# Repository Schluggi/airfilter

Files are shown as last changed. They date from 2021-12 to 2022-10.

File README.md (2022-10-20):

# airfilter 
<a href="https://www.buymeacoffee.com/schluggi" target="_blank">Buy Me A Coffee</a>


> ⚠️ This is a WIP! Some images are missing, but the firmware works fine. 

I've modified my IKEA Förnuftig to work with Home Assistant. After some soldering you can control the filter via MQTT and
also (!) manual with the knob (as originally intended).
I use an ESP32 NodeMCU but an ESP8266 NodeMCU should also work fine.

Via Home Assistant discovery the air filter will show up as a fan-entity with three preset modes `1`, `2` and `3`.
You can also control the fan via the percentage slider.

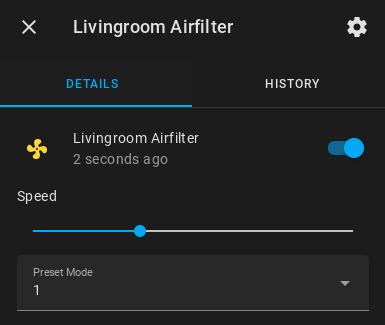
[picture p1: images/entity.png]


## Table of contents
- [Features](https://github.com/Schluggi/airfilter#features)
- [What you need](https://github.com/Schluggi/airfilter#what-you-need)
- [How to](https://github.com/Schluggi/airfilter#how-to)
  - [Flashing](https://github.com/Schluggi/airfilter#flashing)
  - [Teardown](https://github.com/Schluggi/airfilter#teardown)
  - [Soldering and wiring](https://github.com/Schluggi/airfilter#soldering-and-wiring)
- [MQTT](https://github.com/Schluggi/airfilter#mqtt)
- [Home Assistant](https://github.com/Schluggi/airfilter#home-assistant)
- [Questions](https://github.com/Schluggi/airfilter#questions)
- [Credits](https://github.com/Schluggi/airfilter#credits)

## Features
- Control the air filter via MQTT
- Control the air filter manual (as originally intended)
- Home Assistant discovery
  - Support for preset modes
  - Support for percentage control

## What you need
- ESP32 NodeMCU
- 74C14 or 74HC14 Inverter
- 24V to 5V DC/DC-Converter
- Some Jumper Cables
- Superglue
- Soldering iron
- Tiny wires

## How to
### Flashing
Connect the ESP32 NodeMCU via USB to your PC. On Windows you need some additional drivers.
On Linux everything should work out of the box. 
Start the [Arduino IDE](https://www.arduino.cc/en/software) and open the sketch file located at 
`firmware/airfilter/airfilter.ino`.

Change the WiFi and MQTT settings at the top of the file. Then select your NodeMCU (Tools -> Port) and
configure all settings as shown in the screenshot below. Afterwards press flash.
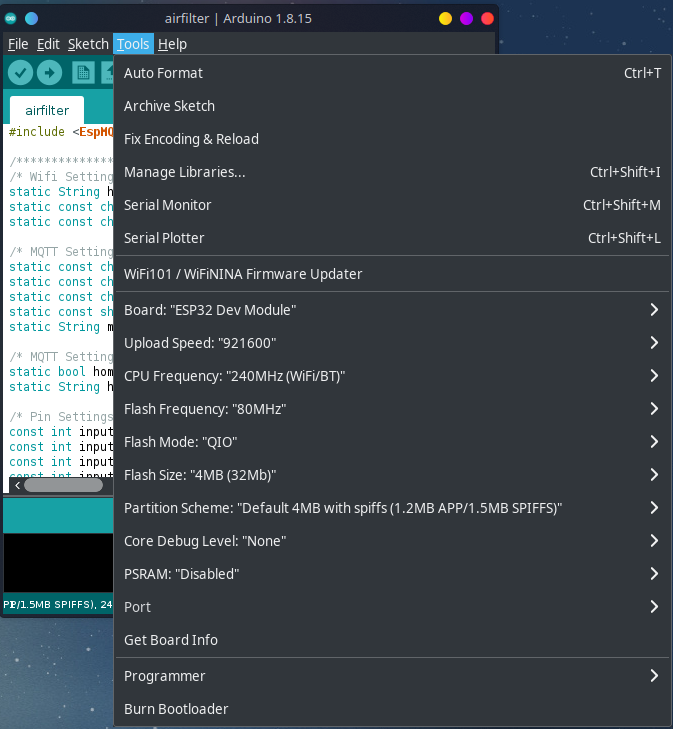
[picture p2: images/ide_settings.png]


### Teardown
Unplug the air filter. 
Remove the blend and the filter. Then unscrew the two phillips screws at the top and remove the plastic part.
Unplug both cables and unscrew the circuit board. You also have to remove the knob before removing the board.

Fortunately IKEA has made a product with a lot of space for us - nice. So we can unscrew the six triangle 
screws and the two phillips screws at the bottom. If you don't have a triangle screwdriver: A slot screwdriver will 
work as well. Then remove the two plastic parts. There are clipped, so make sure not to break anything.
(wip, screw image)

### Soldering and wiring
> **Warning:** This step can not be undone!
 
The knob must not have an effect on the fan speed directly, so we have to cut the circuit path. I've done this with a 
small cutter.
(wip, img cutting)

The internal DC/DC-Converter is sadly not powerful enough to power up the ESP32 (sometimes it works, sometimes not).
So we have to use our own Converter to power up the ESP. Just solder the `GND` and `VIN` pins of the DC/DC-Converter to
the 24V output pin on the circuit board. Connect the `GND` and `VOUT` pins of the DC/DC-Converter to the `VIN` and 
`GND` pins of the ESP.

Connecting the inverter is the hardest part because it's tiny. I've soldered the pins as shown below and then superglued 
the converter onto the board. Not great, but good enough.

#### Wiring
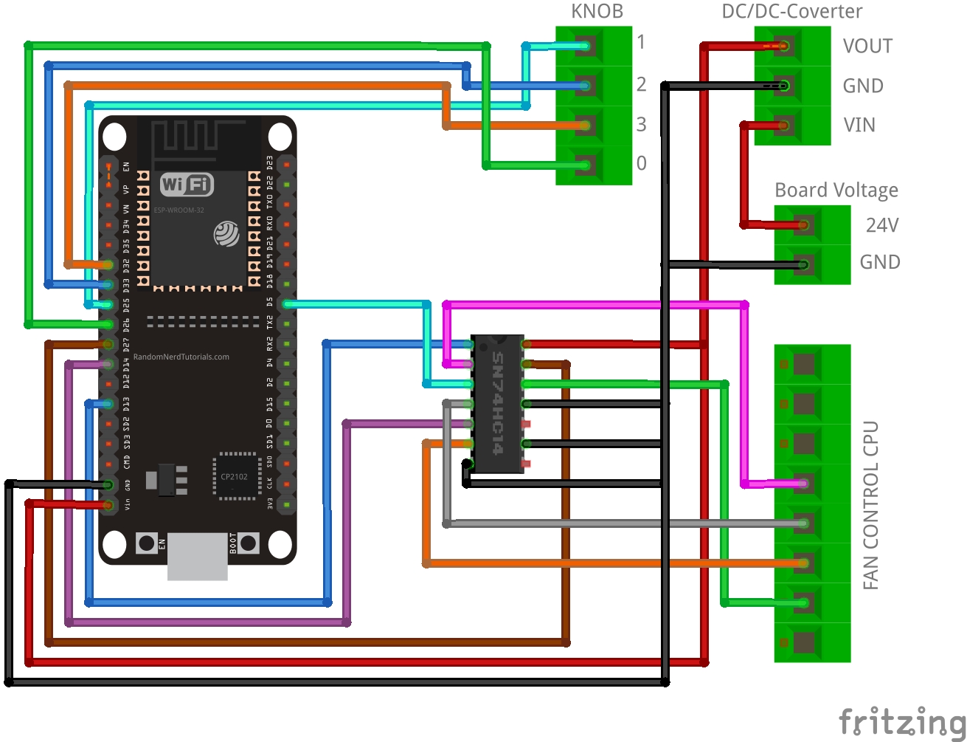
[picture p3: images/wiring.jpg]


This is the fan control CPU. Please mention the origination. 
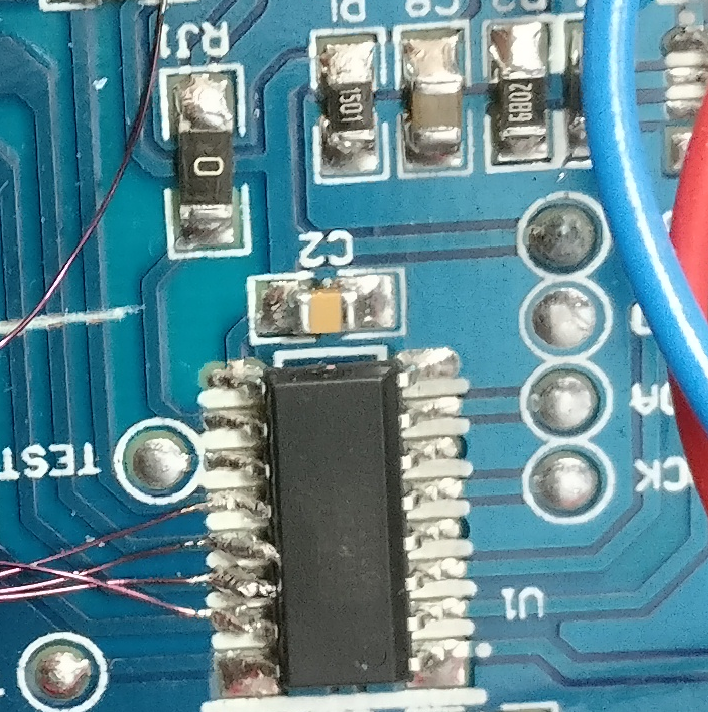
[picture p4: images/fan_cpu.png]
fan_cpu


(wip, img knob connections)

#### Final
> **Caution:** DO NOT USE THIS PHOTO AS REFERENCE! 
> The wiring on this photo looks different from the wiring image because this project
> was learning by doing. So some `GND` and `VCC` wires are connected differently.

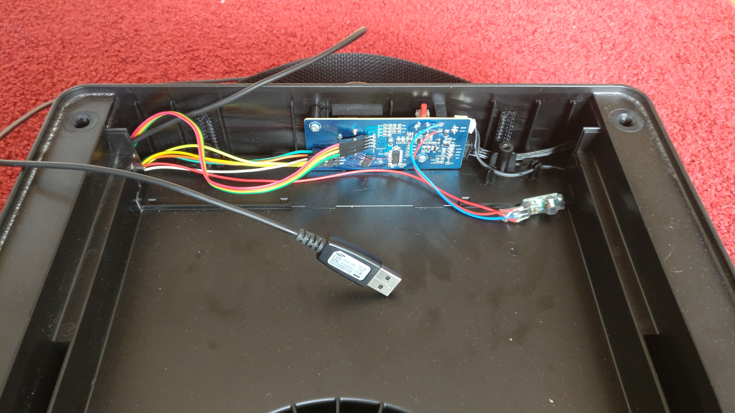
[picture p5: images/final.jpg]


Now we can connect all cables through the hole and place the ESP into the perfect fitting space. I also let the usb cable
connected for future firmware updates. 


## MQTT
> **Additional info:** If you turn off the fan by turning the knob to `0` or by sending the `off` payload, the 
> selected preset mode will not change. 

### On and off
#### `airfilter/<hostname>/state`
Returns the state `on` or `off`, while `off` represents knob position 0.

#### `airfilter/<hostname>/set`
Turn the fan on or off by sending `on` or `off` as payload. 

### Presets
#### `airfilter/<hostname>/preset/state`
Returns the current selected preset mode (`1`, `2` or `3`). This equals the knob position. 
Please also notice the *Additional info*.

#### `airfilter/<hostname>/preset/set`
By sending the payload `0`, `1`, `2` or `3` the fan speed will change like setting the knob to these positions.
`0` will turn off the fan.

### Speed / Percentage
#### `airfilter/<hostname>/speed/state`
Returns the current speed (`0`, `1`, `2` or `3`). This equals the knob position.

#### `airfilter/<hostname>/speed/set`
By sending the payload `0`, `1`, `2` or `3` the fan speed will change like setting the knob to these positions.
`0` will turn off the fan. Analog to _/preset/set_.

## Home Assistant
### Automatic via MQTT discovery (default and recommended)
If you have not disabled MQTT discovery in your Home Assistant instance as well as in the Arduino sketch 
(`homeAssistantMqttDiscovery`). The Fan will show up automatically as a fan entity.



### Manually via config
You can also set up the fan entity manually by adding the following yaml to your Home Assistant `configuration.yaml`:
```yaml
fan:
  - platform: mqtt
    name: "<hostname> Airfilter"
    state_topic: "airfilter/<hostname>/state"
    command_topic: "airfilter/<hostname>/set"
    preset_mode_state_topic: "airfilter/<hostname>/preset/state"
    preset_mode_command_topic: "airfilter/<hostname>/preset/set"
    preset_modes:
       -  "1"
       -  "2"
       -  "3"
    payload_on: "on"
    payload_off: "off"
    percentage_state_topic: "airfilter/<hostname>/speed/state"
    percentage_command_topic: "airfilter/<hostname>/speed/set"    
    speed_range_min: 1
    speed_range_max: 3
```

## Questions
Just open an issue :)

## Credits 
Created and maintained by Lukas Schulte-Tickmann / Schluggi.

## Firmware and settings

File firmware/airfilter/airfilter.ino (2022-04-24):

#include <EspMQTTClient.h>

/****************** CONFIG START *******************/
/* Wifi Settings */
static String hostname = "Livingroom";    //  Unique name for ESP32. The name detected by your router and MQTT.
static const char* ssid = "MyWifi";       //  WIFI SSID.
static const char* password = "12345678"; //  WIFI password.

/* MQTT Settings */
static const char* mqttServerIp = "192.168.1.111";  //  MQTT Broker server ip
static const char* mqttUsername = "";               //  MQTT Broker username. If empty or NULL, no authentication will be used
static const char* mqttPassword = "";               //  MQTT Broker password
static const short mqttServerPort = 1883;           //  MQTT Port
static String mqttMainTopic = "airfilter";          //  MQTT main topic

/* MQTT Settings - Home Assistant */
static bool homeAssistantMqttDiscovery = true;            // Enable to publish Home Assistant MQTT Discovery config
static String homeAssistantMqttPrefix = "homeassistant";  // MQTT Home Assistant prefix

/* Pin Settings */
const int inputPinLevelOff = 26;
const int inputPinLevelOne = 25;
const int inputPinLevelTwo = 33;
const int inputPinLevelThree = 32; 

const int outputPinLevelOff = 13;
const int outputPinLevelOne = 5;
const int outputPinLevelTwo = 14;
const int outputPinLevelThree = 27;
/****************** CONFIG END *******************/

static String mqttTopic = mqttMainTopic + "/" + hostname;
static String lastWillTopic = mqttTopic + "/lastWill";
static String stateTopic = mqttTopic + "/state";
static String commandTopic = mqttTopic + "/set";
static String presetModeCmdTopic = mqttTopic + "/preset/set";
static String presetModeStateTopic = mqttTopic + "/preset/state";
static String precentageCmdTopic = mqttTopic + "/speed/set";
static String precentageStateTopic = mqttTopic + "/speed/state";


static long lastOnlinePublished = 0;

int currentLevel = 0;
int lastLevel = 0;


static EspMQTTClient client(
  ssid,
  password,
  mqttServerIp,
  (mqttUsername == NULL || strlen(mqttUsername)<1) ? NULL : mqttUsername,                    
  (mqttUsername == NULL || strlen(mqttUsername)<1) ? NULL : mqttPassword,
  hostname.c_str(),
  mqttServerPort
);


int getLevel(){
  if ( digitalRead(inputPinLevelOne) && digitalRead(inputPinLevelTwo) && digitalRead(inputPinLevelThree) && !digitalRead(inputPinLevelOff)){
    return 0;
  }
  else if ( !digitalRead(inputPinLevelOne) && digitalRead(inputPinLevelTwo) && digitalRead(inputPinLevelThree) && digitalRead(inputPinLevelOff)){
    return 1;
  }
  else if ( digitalRead(inputPinLevelOne) && !digitalRead(inputPinLevelTwo) && digitalRead(inputPinLevelThree) && digitalRead(inputPinLevelOff)){
    return 2;
  }
  else if ( digitalRead(inputPinLevelOne) && digitalRead(inputPinLevelTwo) && !digitalRead(inputPinLevelThree) && digitalRead(inputPinLevelOff)){
    return 3;
  }

  return -1;
}

void setLevel(int level){
  Serial.println("setting level to: " + String(level));

  if (level) {
    Serial.println("on");
    client.publish(stateTopic.c_str(), "on", true);
    client.publish(presetModeStateTopic.c_str(), String(level), true);
    lastLevel = level;
  } else {
    Serial.println("off");
    client.publish(stateTopic.c_str(), "off", true);
  }
  
  client.publish(precentageStateTopic.c_str(), String(level), true);
  
  switch (level) {
    case 0:
      digitalWrite(outputPinLevelOff, HIGH);
      digitalWrite(outputPinLevelOne, LOW);
      digitalWrite(outputPinLevelTwo, LOW);
      digitalWrite(outputPinLevelThree, LOW);
      break;
    case 1:
      digitalWrite(outputPinLevelOff, LOW);
      digitalWrite(outputPinLevelOne, HIGH);
      digitalWrite(outputPinLevelTwo, LOW);
      digitalWrite(outputPinLevelThree, LOW);
      break;
    case 2:
      digitalWrite(outputPinLevelOff, LOW);
      digitalWrite(outputPinLevelOne, LOW);
      digitalWrite(outputPinLevelTwo, HIGH);
      digitalWrite(outputPinLevelThree, LOW);
      break;
    case 3:
      digitalWrite(outputPinLevelOff, LOW);
      digitalWrite(outputPinLevelOne, LOW);
      digitalWrite(outputPinLevelTwo, LOW);
      digitalWrite(outputPinLevelThree, HIGH);
      break;      
  }
}


void onConnectionEstablished(){  
  // home assistnat discovery
  if (homeAssistantMqttDiscovery){
    String payload = "{\"name\":\"" + hostname + " Airfilter\",\"stat_t\":\"airfilter/" + hostname + "/state\",\"cmd_t\":\"airfilter/" + hostname + "/set\",\"pr_modes\":[\"1\",\"2\",\"3\"],\"pr_mode_cmd_t\":\"airfilter/" + hostname + "/preset/set\",\"pr_mode_stat_t\":\"airfilter/" + hostname + "/preset/state\",\"pl_on\":\"on\",\"pl_off\":\"off\", \"pct_stat_t\":\"airfilter/" + hostname + "/speed/state\", \"pct_cmd_t\":\"airfilter/" + hostname + "/speed/set\", \"spd_rng_min\":\"1\", \"spd_rng_max\":\"3\"}";
    client.publish(homeAssistantMqttPrefix + "/fan/" + hostname + "/config", payload, true);
  }
  
  // preset modes
  client.subscribe(presetModeCmdTopic.c_str(), [] (const String& payload){
    Serial.println("preset_mode received: " + payload);  
    setLevel(payload.toInt());
  });
 
  // speed / percentage
  client.subscribe(precentageCmdTopic.c_str(), [] (const String& payload){
    Serial.println("speed received: " + payload);
    setLevel(payload.toInt());
  });
  
  // on & off / state
  client.subscribe(commandTopic.c_str(), [] (const String& payload){
    Serial.println("command received: " + payload);  
    if (payload == "on"){
      setLevel(lastLevel);
    } else {
      setLevel(0);
    }
  });
}
  
void setup() {  
  Serial.begin(115200);
  Serial.println("Booted!"); 

  // setup mqtt
  client.setMqttReconnectionAttemptDelay(100);
  client.enableLastWillMessage(lastWillTopic.c_str(), "offline");
  client.setKeepAlive(60);
  client.setMaxPacketSize(1024);

  // setup output pins
  pinMode(outputPinLevelOff, OUTPUT);
  pinMode(outputPinLevelOne, OUTPUT);
  pinMode(outputPinLevelTwo, OUTPUT);
  pinMode(outputPinLevelThree, OUTPUT);

  // setup input pins
  pinMode(inputPinLevelOff, INPUT_PULLUP);
  pinMode(inputPinLevelOne, INPUT_PULLUP);
  pinMode(inputPinLevelTwo, INPUT_PULLUP);
  pinMode(inputPinLevelThree, INPUT_PULLUP);

  // set startup level
  setLevel(getLevel());
}

void loop() {
  // starting mqtt client
  client.loop();

  // update last will every 30s
  if ((millis() - lastOnlinePublished) > 30000) {
    if (client.isConnected()) {
      client.publish(lastWillTopic.c_str(), "online", true);
      lastOnlinePublished = millis();
    }
  }
  
  // check for knob overwrites
  int newLevel = getLevel();
  if (newLevel != currentLevel && newLevel != -1){
    currentLevel = newLevel;
    setLevel(newLevel);
  }
  
  delay(100);
}

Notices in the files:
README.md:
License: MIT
